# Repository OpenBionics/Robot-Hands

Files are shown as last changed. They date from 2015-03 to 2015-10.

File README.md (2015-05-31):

# Overview

OpenBionics is an initiative for the development of:
* open source
* affordable
* light-weight
* modular

robot hands and myoelectric prosthetic devices, that can be easily reproduced using off-the-shelf materials.

This repository contains all the necessary files, to replicate our robot hands.

For more information visit [OpenBionics.](http://www.openbionics.org/)

We have published a complete tutorial for the replication of our hands. The tutorial can be found [here.](http://www.openbionics.org/TR2015_OpenBionics_RobotHandsGuide.pdf)

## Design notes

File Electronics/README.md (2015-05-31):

# Electronics

This folder presents the electronics for the robot hands and for the interfaces (the Schematic, the PCB Layout and the OpenBionics library).
In order to control the RC or the AX12 servo motor, we use the arduino Micro Pro microcontroller platform, combined with a custom "Shield".

More information about Arduino Micro can be found [here.](http://arduino.cc/en/Main/ArduinoBoardMicro)

# Pinout
The Pin Mapping of the Arduino Micro Pro "Shield".



# Build of Materials of main PCB
	Part           Value              Device             Package 
	ARDUINO_MICRO  -                  -		     -
	C1             100u               CPOL-EUE2.5-6      E2,5-6  
	IC1            74LS241N           74LS241N           DIL20 
	J1             -                  HEADER-2X3P-2.54   -
	J2             SCREW-TERMINAL-2P  SCREW-TERMINAL-2P  -
	J3             -                  HEADER-2P-65/35MIL -          
	J4             -                  HEADER-2P-65/35MIL -    
	R1             10k                RESISTOR1206       1206
	R2             10k                RESISTOR1206       1206
	R3             10k                RESISTOR1206       1206
	S1             -                  SWITCH-SPDTSMD2    -  

# Mount PCB in to Robot Hands

You can attach the PCB at the PCBMount.STL part of the robot hands, using two M2x8 screws and two M2 nuts.



# Interfaces

#####RobotHandExtension
This interface requires push buttons and wires with the appropriate terminals.
The push buttons are placed in suitable pockets in RobotHandExtension part. Moreover, the  RobotHandExtension part has the necessary routing for the wires. The open button pin is B1 and it is placed on the top of the RobotHandExtension part. The close button pin is B2 and it is placed on the right hand side of the same part.

######Build of Materials
    2x push buttons
    2x wires terminals for HEADER-2P-65/35MIL (HEADER-2P)

#####SliderBox
This interface requires one arduino board and two linears potentiometers.
The potentiometers are connected to the analog inputs A0 and A1 of arduino board.

######Build of Materials
    2x linear potentiometer 10k (linear)
    1x Arduino board
    1x Jumper Wire Pack

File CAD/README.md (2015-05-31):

# Robot Hands CAD files

In this folder we provide appropriate 3D models (Solidworks .SLDASM .SLDPRT), laser cut files (.dxf) and files for 3d printer (.stl)
in order to replicate the proposed designs.

# Design and Fabrication Parameters

The designs of parts (Solidworks .SLDASM .SLDPRT) are parametric. Thus, the user could choose the appropiate dimensions that he wants.
A guide by which inspired is [here](http://www.eng.yale.edu/grablab/openhand/OpenHand%20CAD%20Guide.pdf). The picture below and tables
show the parameters and limits of the values. 



#####Design Parameters
	Name of parameter: limits, default value
	Width of Phalanxs, Wph (mm): 16 - 30, 20
	Length of Proximal Phalanx, Lp (mm): 24 - , 40
	Length of Distal Phalanx, Ld (mm): 18 - , 35
	Transmission radii of Proximal, rp (mm): 7.8 - , 8
	Transmission radii of Distal, rd (mm):7.8 - , 8
	Thickness of Proximal Flexure Joint, Tjointp (mm): 2 - 6, 4
	Thickness of Distal Flexure Joint, Tjointd (mm): 2 - 6, 5
	Length of Proximal Flexure Joint, Ljointp (mm): 6 - 16, 10
	Lenght of Distal Flexure Joint, Ljointd (mm): 6 - 16, 10
	Width of flexure Joints, Wjoint (mm): 16 - 30, 20
	Initial angle between Finger Base and robot Base, Tb (degrees): 20 - 45, 45
	Initial angle between Finger Base and Proximal, Tp (degrees): 0 - 30, 8
	Initial angle between Proximal and Distal, Td (degrees): 0 - 30, 8
	Finger opposition length, Lb (mm): 45 - 55, 45

#####Fabrication Parameters
	print fit, print_fit (mm): 0.2
	print free, print_free (mm): 0.45
	cut free, cut_free (mm): 0.2
	radii fit, radii_fit (mm): 0.2

In order to print or cut the parts in correct dimensions is necessary to add in design the above parameters.

More information about the fabrication parameters you can find [here for 3d printer](http://www.eng.yale.edu/grablab/openhand/OpenHand%20CAD%20Guide.pdf) and [here for laser cutter](http://support.ponoko.com/entries/498833-How-to-make-interlocking-acrylic-designs).

# Robot Finger Structure


# Replicating the Robot Hand Design

In order to replicate this design of robot hands, you will need the below materials.

    [1] 2mm Acrylic Parts or 3D printed Parts
	[2] Fasteners 
	[3] Cotton Swabs 
	[4] Silicone sheets 
	[5] Dyneema Fishing Line 
	[6] Rubber Foam tape 
	[7] Anti-Slip Tape 
	[8] Self-Adhesive Tape
	[9] Long Darners 
	[10] Nylon Fishing Line (not shown in the image)
	


For more information about [design](http://www.openbionics.org/?page_id=38)

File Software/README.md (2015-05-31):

# Introduction

<p style='text-align: justify;'>
In order to control the robot hand, we use the Robot Operating System (ROS) and arduino micro board.
The Planner PC runs one ROS node (RobotHand.py), that is responsible for sending commands, for parsing the data packages which are send by 
arduino micro and for publishing the received information in the ROS topics.
The arduino micro is responsible to parse the planner pc commands, to drive the different servo motors and is respond to the planner pc with
the information about robot hand.
</p>

# ROS Installation

Install this ROS package placing the folder in the /src directory of your ROS workspace. Build the package using the following command:

    $catkin_make

You have successfully installed the package. Make sure that all files are executable, using the following command:

     $chmod +x RobotHand.py

# Arduino Installation

Donwload the [arduino IDE](http://arduino.cc/en/main/software).
Place the [library for dynamixel servo](https://github.com/OpenBionics/Robot-Hands/tree/master/Software/Arduino/Libraries/DynamixelSerial) in 
your library folder. 
Place the RobotHand folder in your arduino workspace.
Open the RobotHand.ino with arduino IDE.
Select with MODE definition the servo motor that you use:

    #define MODE 1 :is for stadard RC servo
    #define MODE 2 :is for dynamixel AX12 servo

Upload the program to the arduino Micro board.

# How to run ROS node

To run this ROS package, you have to run the launch file:

    $roslaunch openbionics RobotHand.launch

In the launch file you can set up the USB port, to establish serial communication with the robot hand. It is necessary to give write permissions
on that port. The RobotHand node listen to RobotHandCmd topic and send those commands to arduino board via serial. The robot hand responds with 
sending back to the host pc the acknowledgement and the state of servo motor (depending to the sending command). The RobotHand node publish the 
acknowledgment in the RobotHandAck topic and the state of motor in MotorState topic.
If the acknowledgment is 0 means that robot hand receives acceptable command, but if it is -1 means that you have send wrong command. The motor 
state package has the following format:
    
    acknowledgment;angle (deg);load (0-1023 for CCW, 1024-2047 for CW)\n

# How to control the robot hand

To control the robot hand you can use the following command:

    $rostopic pub -1 /RobotHandCmd openbionics/Command "cmd: 'arg'" 

Replace the arg: 

    ps "angle in deg", the angle depends on the servo motor
    vl "velocity in deg/s", the velocity depends on the servo motor
    gs, to get the state of servo motor

In order to view the acknowledgment and the state of motor you can use the following commands:

	$rostopic echo /MotorState
	$rostopic echo /RobotHandAck

# Interfaces

It is not necessary to use the planner PC for the control of the robot hand. The user could also use the proposed interfaces.

#####RobotHandExtension
The firmware for RobotHandExtension interface is inside in RobotHand.ino and is active:

    #define EXTENSION 1: with RobotHandExtension interface 

and deactive:

    #define EXTENSION 0: without RobotHandExtension interface

#####SliderBox
The SliderBox interface requires the use of planner PC. The ROS node that reads the commands from SliderBox writes in RobotHandCmd topic.
Also, with this interface an additional arduino is needed. The firmware for arduino is placed in Arduino/SliderBox.
In order to run SliderBox ROS node, make sure that it is executable, using the following command:

     $chmod +x SliderBox.py

and run it:

    $rosrun openbionics SliderBox.py "usb port" (e.g /dev/ttyACM0)

Before you execute the above command, you must run the launch file as mentioned above (How to run ROS node), and to give write
permissions on that port.

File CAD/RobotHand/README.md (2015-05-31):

# Physical Characteristics of Robot Finger and Hand
###Robot Finger:


    DOF's: 2
	Width(mm): 20
	Lenght(mm): 95
	Weigth(g): 20 
	Force in fingertip (N): 8
	
###Robot Hand:


	Actuators: 1
	Base Height(mm): 100-110
	Base Width(mm): 77
	Weight(g): 280
	Number of Fingers: 2-4

To change the design or fabrication parameters you must change the dimensions of the RobotHandParameters.SLDPRT sketch.

A complete tutorial for the replication of this robot hand can be found
[here.](http://www.openbionics.org/TR2015_OpenBionics_RobotHandsGuide.pdf)

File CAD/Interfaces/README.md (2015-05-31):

# Robot Hands Interfaces
In order to control robot hands the user can use the proposed interfaces.
#####Robot Hand Extension: 
This interface had two buttons, one for closing and one for opening the robot hand. 
To make this, you should print with 3d printer two parts, RobotHandExtension.STL and dovetail_male_RobotHandExtension.STL.
For connecting the two parts you must use a M5 nut and screw which you can find at common parts folder.
######Build of Materials
    1x M5 Nut
    1x M5 L22
    ABS Filament

#####SliderBox:
This interface had two linear potentiometers. Until now the one of these are active.
Also, SliderBox could be use for robot hands which had two servo motors like
[Model T42  of Yale OpenHand Project](http://www.eng.yale.edu/grablab/openhand/model_t42.html#performance).
To make this, you should cut the parts, which are in /dxf folder, in acrylic sheet with laser cutter. For connecting the parts you must use 
glue for acrylic, M3 nuts and screws. For connecting the potentiometers in the
SliderBox you must use M3 nuts, screws and spacers which are in common parts folder. 
######Build of Materials
    14x M3 Nut
    6x M3 L8
    8x M3 L20
    8x plastic spacers L15 for M3 screw
    Glue for Acrylic
    Acrylic sheet 2mm
    
For both interfaces you can find the software, firmware and electronics in respective folders of Robot-Hands repo.

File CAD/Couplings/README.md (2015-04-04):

# Couplings

The designs of Mount_Kuka-Youbot.SLDPRT, dovetail_famele.SLDPRT and dovetail_made.SLDPRT are taken from [Yale Openhand Project](https://github.com/grablab/openhand-hardware/tree/master/couplings), thank you!

The design of MountPA10.SLDASM is specific for our flange for the Mitsubishi PA10 robotic arm.

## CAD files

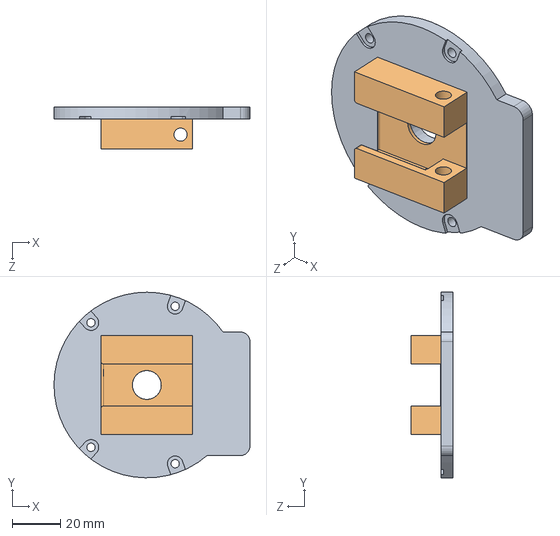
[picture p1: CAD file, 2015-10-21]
CAD/RobotHand/3d Printed/Robot Base/FlangeCoupling.SLDASM
81.3 x 77.0 x 17.5 mm
FlangePlate
dovetail_female

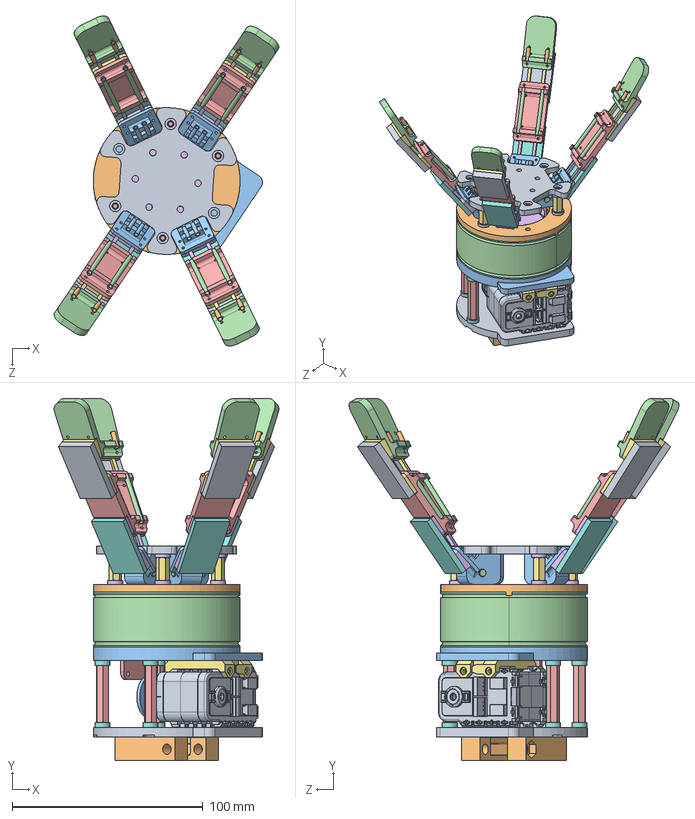
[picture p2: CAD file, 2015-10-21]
CAD/RobotHand/3d Printed/RobotHand.SLDASM
117.9 x 190.0 x 173.1 mm
TopPlate
MiddlePlate
BottomPlate
93600A129 - DowelPinM4L12 x 5
PCBMount
DifferentialDisk
AX12Base
ax12_wheel
ax12_box
ax12_cog
servoPulleyAX12
94868A181 - HexStandoffM3L30 x 8
Spacer - 2mm x 8
94868A007 - HexStandoffM3L12 x 4
Spacer - 2_5mm x 8
FlangePlate
dovetail_female
FingerBase x 4
FingerDIP x 4
FingerPIP x 4
JointBase1 x 4
JointBase2 x 4
Joint1 x 4
Joint2 x 4
tubeDIP x 8
tubeMCP x 8
tubePIP x 8

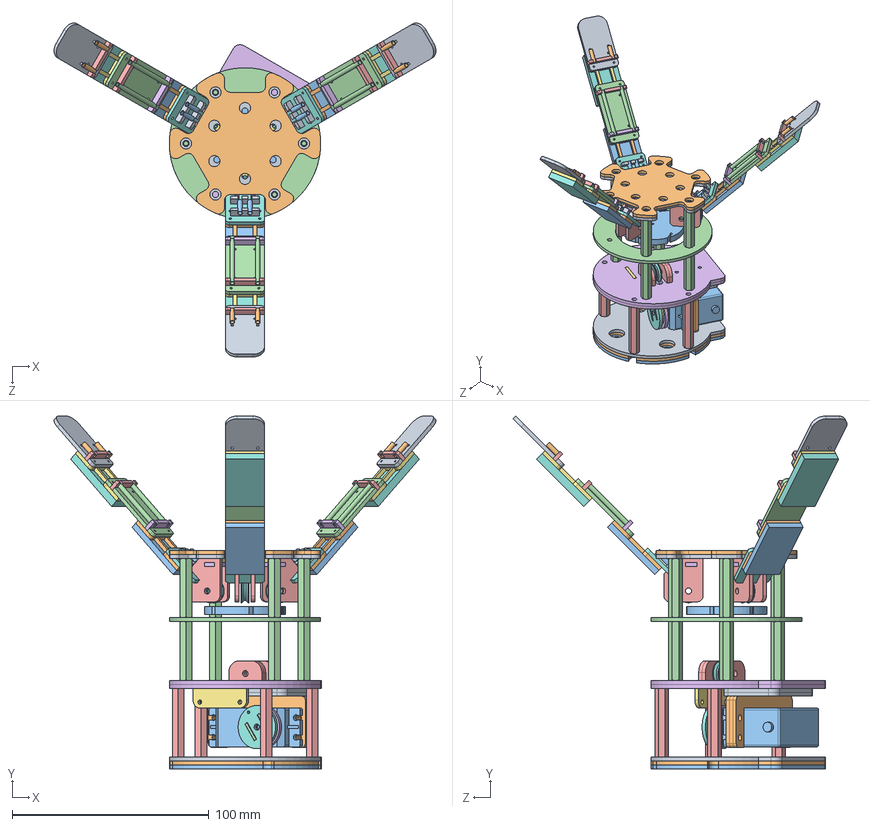
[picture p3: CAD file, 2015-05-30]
CAD/RobotHand/Laser Cutted/RobotHand.SLDASM
194.3 x 179.5 x 169.9 mm
TopPlate1
TopPlate2
DifferentialDisk
MiddlePlate
BearingBase x 4
BottomPlate x 2
PCBMount
pulley x 4
MountPA10_1
MountPA10_2
MountPA10_3
94868A181 - HexStandoffM3L30 x 8
94868A184 - HexStandoffM3L35 x 4
servoPulleyStd1
servoPulleyStd2
servoPulleyStd3
stdServoBase1 x 2
stdServoBase2 x 3
HS-422
ServoHorn
FingerBase1 x 6
FingerBase2 x 3
FingerBase3 x 3
FingerMCP x 3
TubePlateMCP x 6
JointBase1 x 3
Joint1 x 3
FingerPIP x 3
TubePlateDIP x 6
TubePlatePIP x 3
JointBase2 x 3
Joint2 x 3
FingerDIP x 3
tubeDIP x 6
tubeMCP x 6
tubePIP x 6

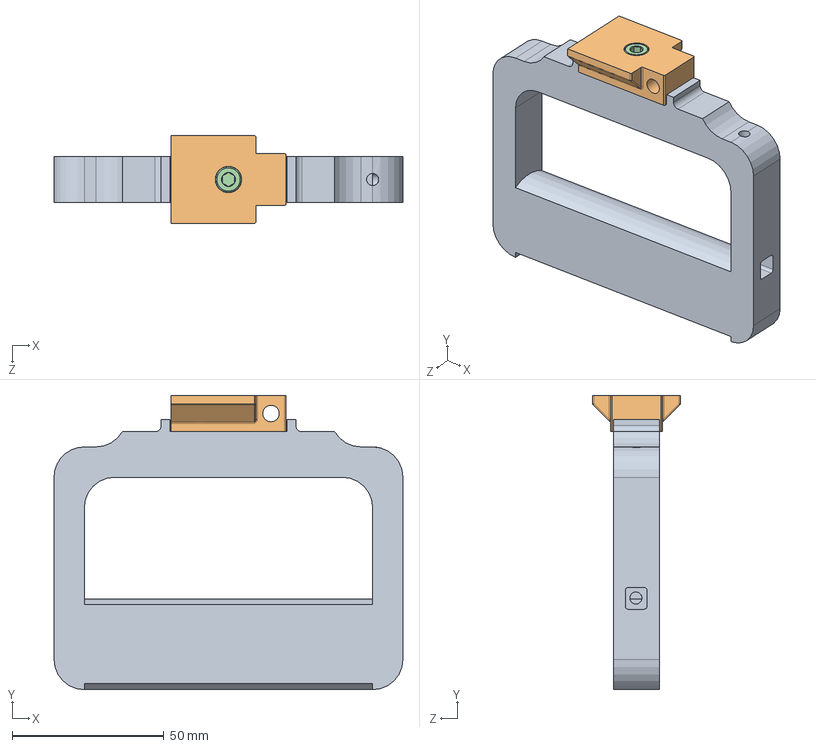
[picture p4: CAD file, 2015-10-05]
CAD/Interfaces/Extension/RobotHandExtensionAssembly.SLDASM
115.0 x 97.0 x 29.0 mm
RobotHandExtension
dovetail_male_RobotHandExtension
91828A241 - NutM5
92290A782 - ScrewM5L22

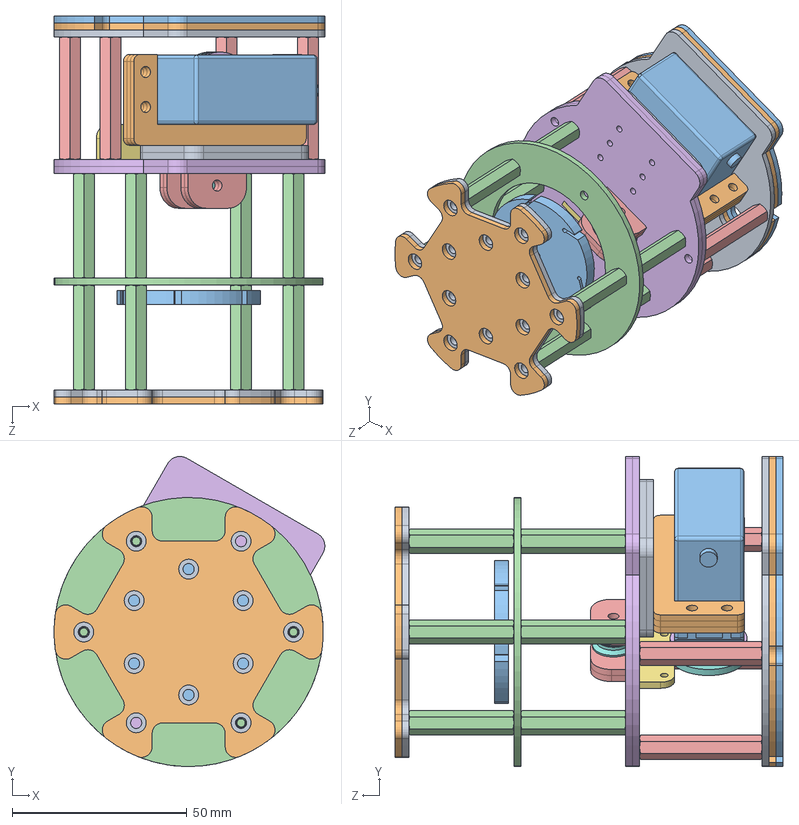
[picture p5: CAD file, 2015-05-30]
CAD/RobotHand/Laser Cutted/Robot Base/Base.SLDASM
77.5 x 88.8 x 111.0 mm
TopPlate1
TopPlate2
DifferentialDisk
MiddlePlate
BearingBase x 4
BottomPlate x 2
PCBMount
pulley
MountPA10_1
MountPA10_2
MountPA10_3
94868A181 - HexStandoffM3L30 x 8
94868A184 - HexStandoffM3L35 x 4
servoPulleyStd1
servoPulleyStd2
servoPulleyStd3
stdServoBase1 x 2
stdServoBase2 x 3
HS-422
ServoHorn

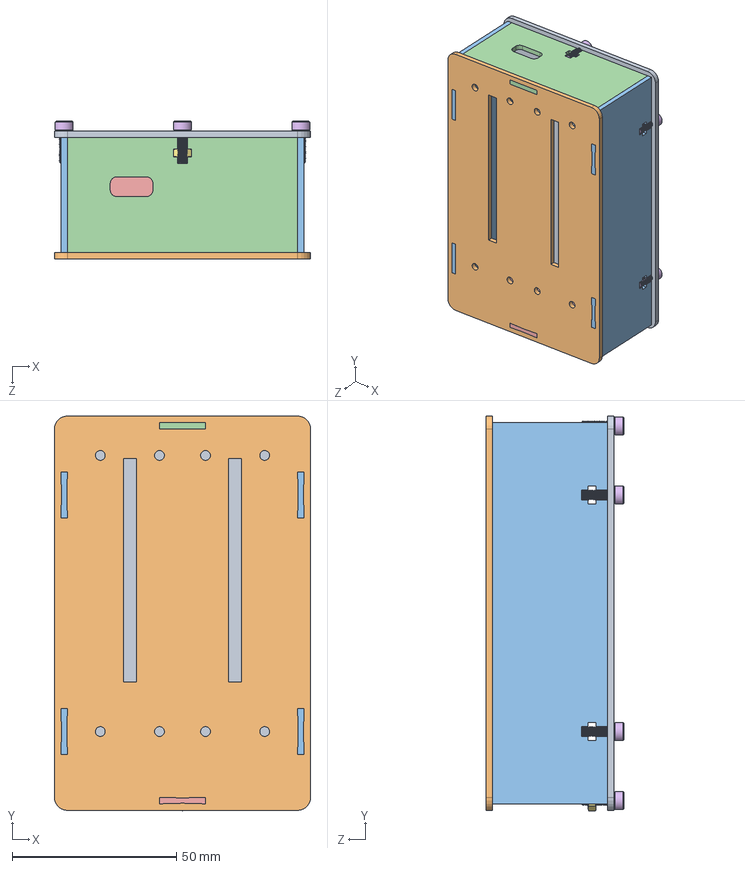
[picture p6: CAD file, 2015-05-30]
CAD/Interfaces/SliderBox/SliderBox.SLDASM
78.0 x 120.2 x 42.0 mm
SliderBottom
SliderTop
SlideSide x 2
SlideSideUp
SlideSideDown
92290A115 - ScrewM3L10 x 6
94150A325 - NutM3

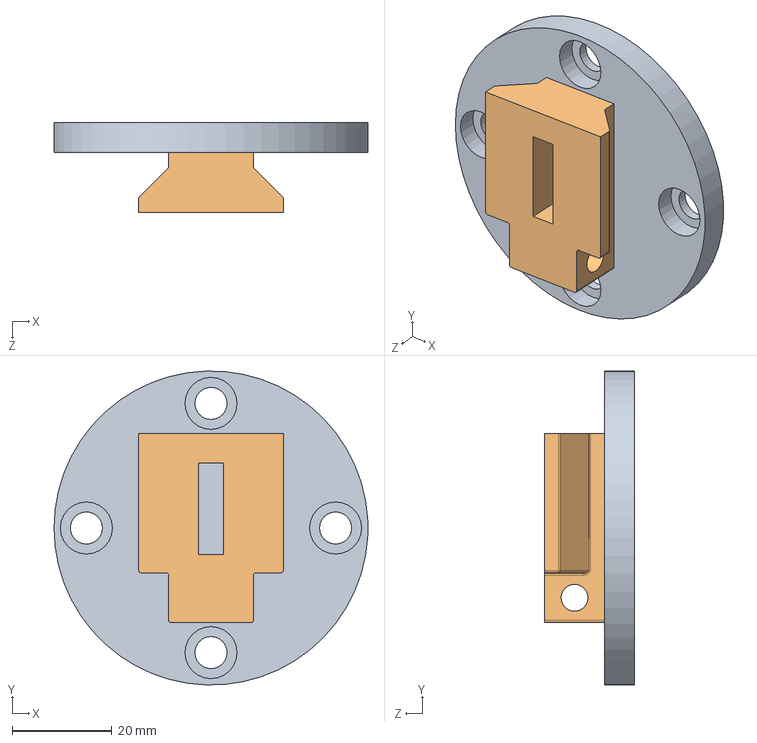
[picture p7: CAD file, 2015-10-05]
CAD/Couplings/MountPA10.SLDASM
63.0 x 63.0 x 18.0 mm
MountPlatePA10
dovetail_male

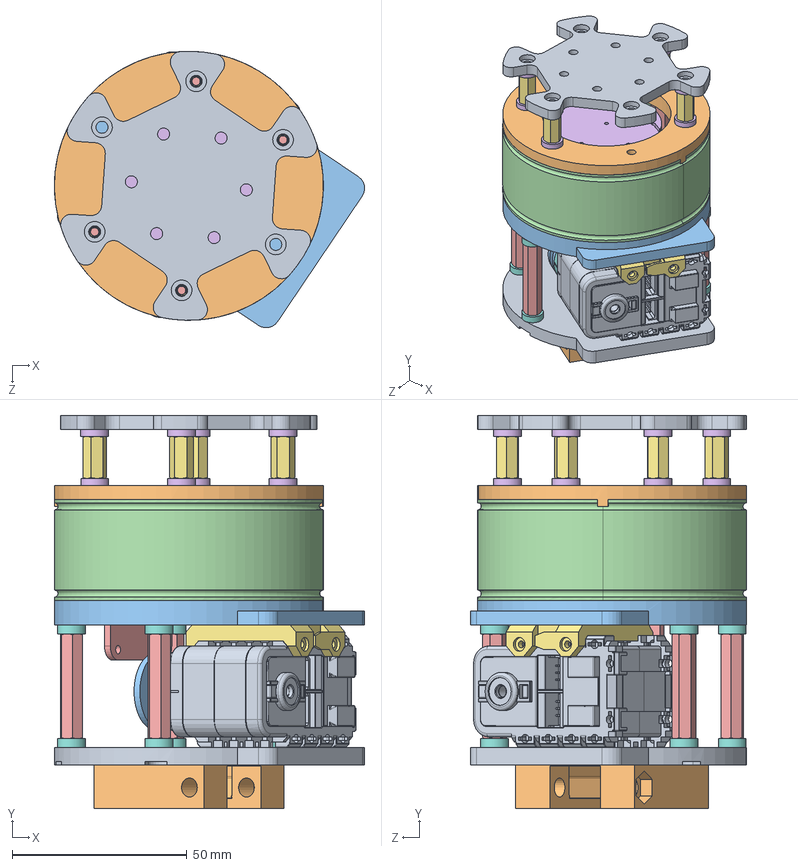
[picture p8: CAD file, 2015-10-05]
CAD/RobotHand/3d Printed/Robot Base/Base.SLDASM
88.8 x 112.5 x 79.1 mm
TopPlate
MiddlePlate
BottomPlate
93600A129 - DowelPinM4L12
PCBMount
DifferentialDisk
AX12Base
ax12_wheel
ax12_box
ax12_cog
servoPulleyAX12
94868A181 - HexStandoffM3L30 x 8
Spacer - 2mm x 8
94868A007 - HexStandoffM3L12 x 4
Spacer - 2_5mm x 8
FlangePlate
dovetail_female

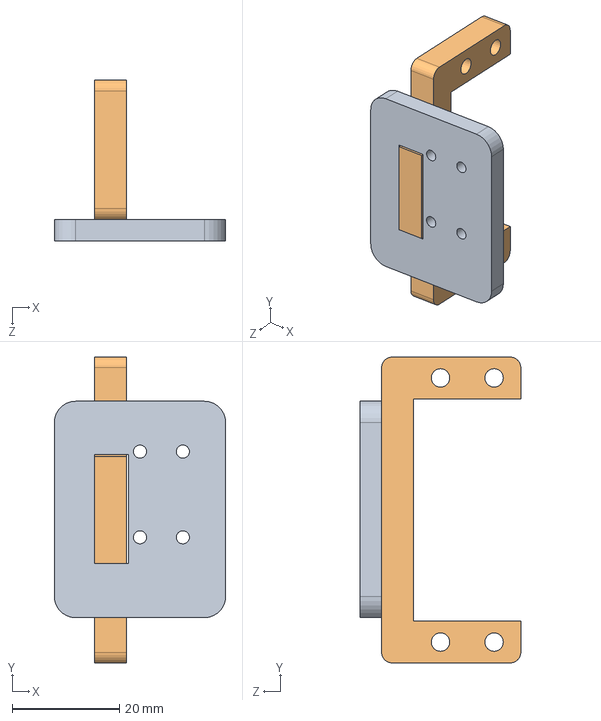
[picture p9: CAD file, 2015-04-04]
CAD/RobotHand/3d Printed/Robot Base/stdServoBase.SLDASM
32.0 x 57.1 x 30.0 mm
stdServoBase1
stdServoBase2

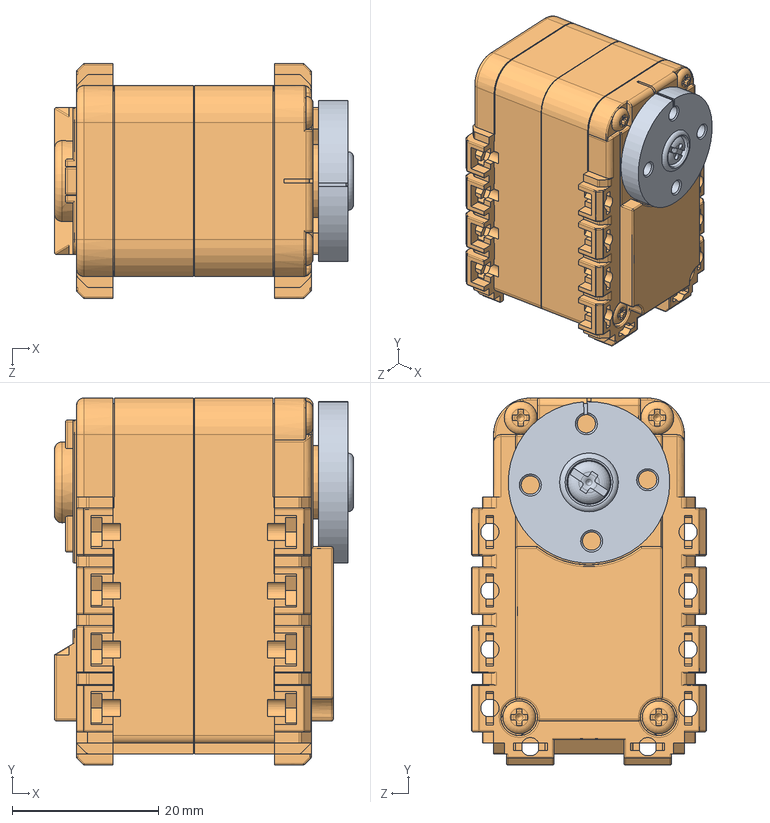
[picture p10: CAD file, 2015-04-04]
CAD/Common Parts/AX12.SLDASM
40.8 x 50.0 x 32.0 mm
ax12_wheel
ax12_box
ax12_cog

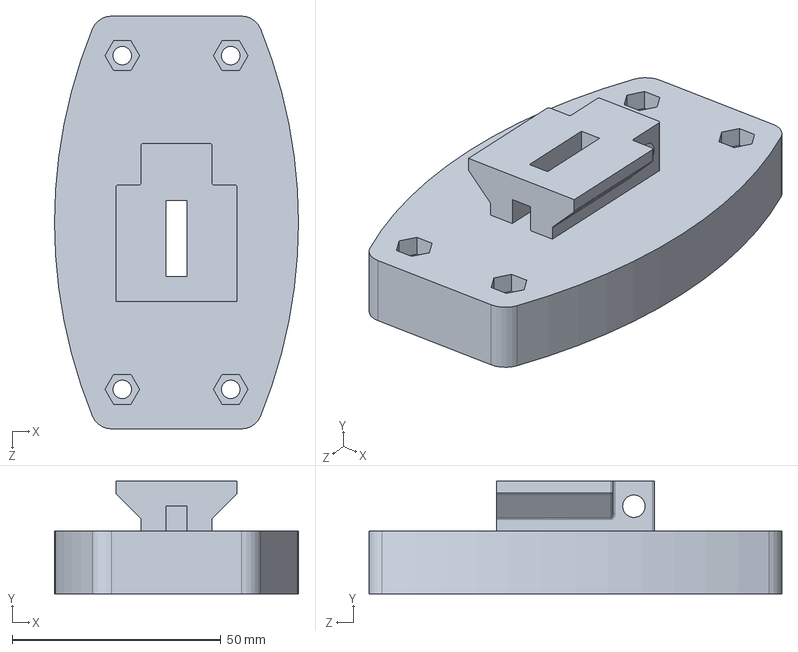
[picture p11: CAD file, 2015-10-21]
CAD/Couplings/Mount_Kuka-Youbot.SLDPRT
58.5 x 27.0 x 99.0 mm

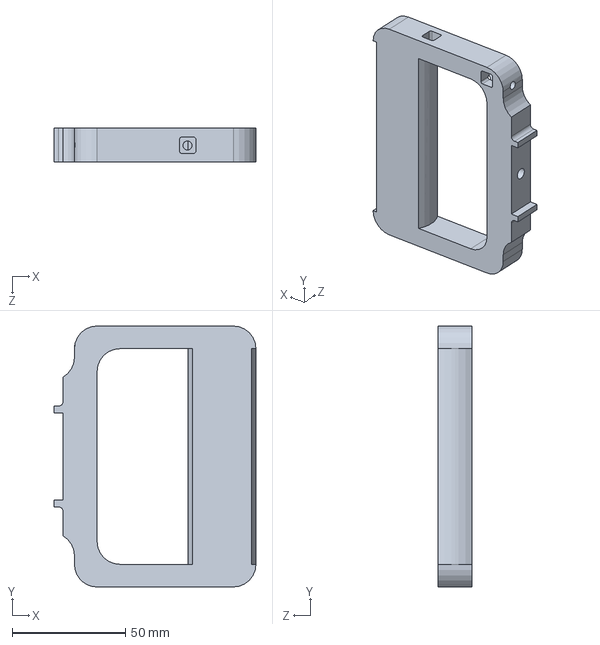
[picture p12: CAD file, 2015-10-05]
CAD/Interfaces/Extension/RobotHandExtension.SLDPRT
89.0 x 115.0 x 15.0 mm

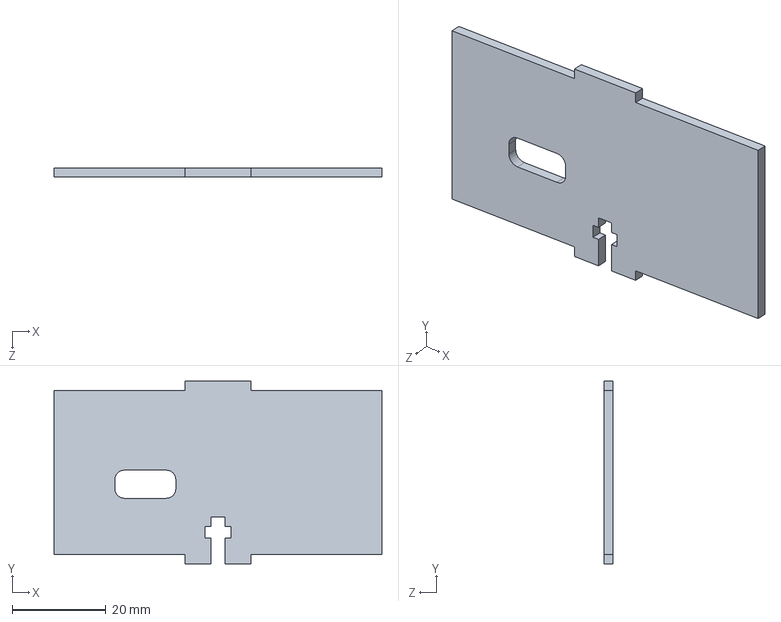
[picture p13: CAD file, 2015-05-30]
CAD/Interfaces/SliderBox/SlideSideUp.SLDPRT
70.0 x 39.0 x 2.00 mm

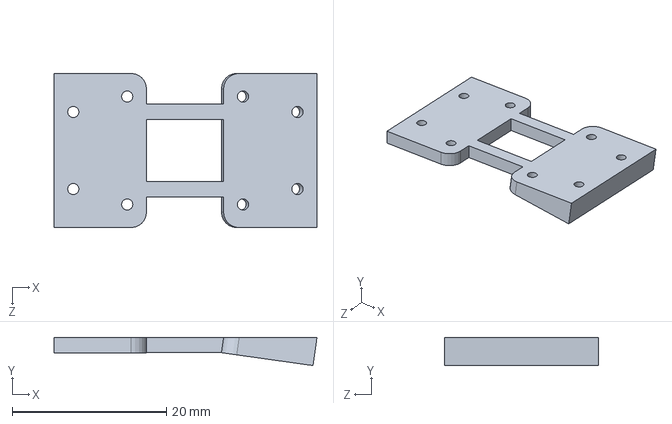
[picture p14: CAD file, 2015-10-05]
CAD/RobotHand/3d Printed/Robot Finger/JointBase2.SLDPRT
34.1 x 3.65 x 20.0 mm

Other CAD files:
CAD/FabricationParameters.SLDPRT
CAD/RobotHand/Laser Cutted/Robot Base/TopPlate1.SLDPRT
CAD/RobotHand/Laser Cutted/Robot Finger/FingerBase3.SLDPRT
CAD/RobotHand/RobotHandParameters.SLDPRT
CAD/Common Parts/90666A131 - ScrewM6L12LowProfile.SLDPRT
CAD/Common Parts/90965A130 - WasherM3.SLDPRT
CAD/Common Parts/91290A123 - ScrewM3L20.SLDPRT
CAD/Common Parts/91292A114 - ScrewM3L12.SLDPRT
CAD/Common Parts/91292A195 - ScrewM5L45.SLDPRT
CAD/Common Parts/91292A831 - ScrewM2L6.SLDPRT
CAD/Common Parts/91292A832 - ScrewM2L8.SLDPRT
CAD/Common Parts/91292A833 - ScrewM2L10.SLDPRT
CAD/Common Parts/91828A241 - NutM5.SLDPRT
CAD/Common Parts/92290A113 - ScrewM3L8.SLDPRT
CAD/Common Parts/92290A115 - ScrewM3L10 .SLDPRT
CAD/Common Parts/92290A745 - ScrewM2L4.SLDPRT
CAD/Common Parts/92290A782 - ScrewM5L22.SLDPRT
CAD/Common Parts/92605A109 - NonmarringM3L20.SLDPRT
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

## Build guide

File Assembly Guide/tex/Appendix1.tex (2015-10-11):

\section{Necessary Tools and Materials}

In this section we present the necessary tools and materials for the construction and assembly of the different robot hand parts. All tools and materials used, can be easily found in hardware stores around the world.

\begin{center}
\begin{tikzpicture}
\node [mybox] (box){
	\begin{tabular}{ c c }
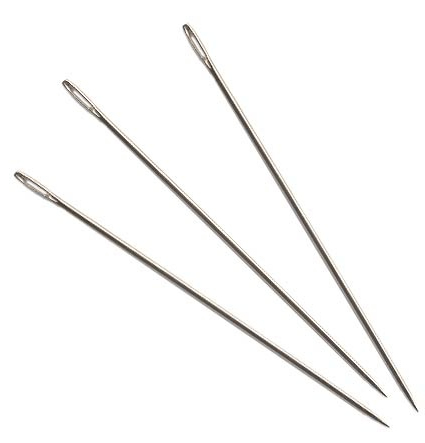
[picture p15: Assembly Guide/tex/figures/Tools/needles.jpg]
		 &
		 
		\\
		Long Darners [D:1mm, L:70mm] & Precision Ruler
		\\
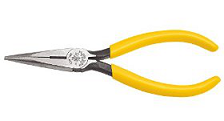
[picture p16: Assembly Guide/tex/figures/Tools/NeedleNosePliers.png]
		 &
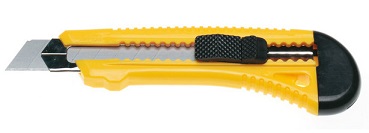
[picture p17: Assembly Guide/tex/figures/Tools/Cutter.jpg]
		 
		\\
		 Long-Nose Pliers with Side-Cutting & Cutter
		\\
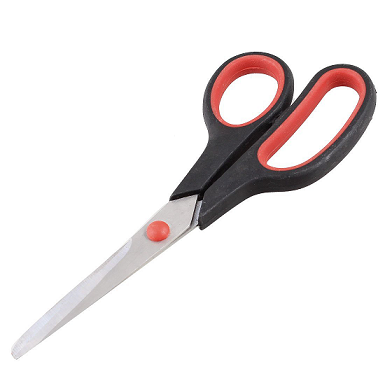
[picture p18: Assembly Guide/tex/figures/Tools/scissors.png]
		 &
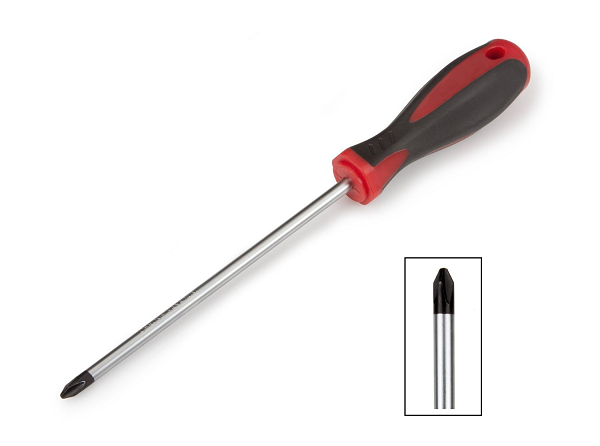
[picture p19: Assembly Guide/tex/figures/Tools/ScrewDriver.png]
		
		\\
		Scissors & Phillips Screwdriver [no. 1,2]
		\\
		 &
		
		\\
		Open-End Wrench [M2, M3 Hex Nut] & Allen Wrench [2.5mm]		
		\\
    	\end{tabular}
};
\node[mytitle, right=10pt] at (box.north west) {Tools};
\end{tikzpicture}%
\end{center}

\begin{center}
\begin{tikzpicture}
\node [mybox] (box){
	\begin{tabular}{ c c c }
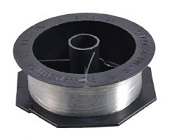
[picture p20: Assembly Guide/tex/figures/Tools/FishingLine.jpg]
		 &
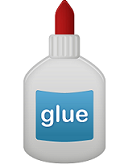
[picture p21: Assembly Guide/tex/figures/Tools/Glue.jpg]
                 &
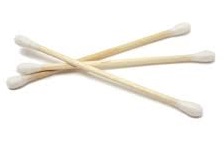
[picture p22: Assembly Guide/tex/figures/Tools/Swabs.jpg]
                \\
		Dyneema Fishing Line [0.4mm] & Acrylic Glue \& Super Glue & Ear Cotton Swabs\\
		\& Nylon Fishing Line [0.4mm] & & \\
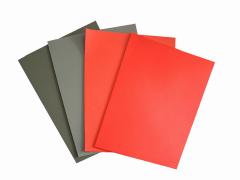
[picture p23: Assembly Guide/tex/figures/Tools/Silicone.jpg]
		 &
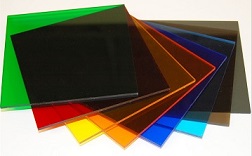
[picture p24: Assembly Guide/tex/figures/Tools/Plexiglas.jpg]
                 & 
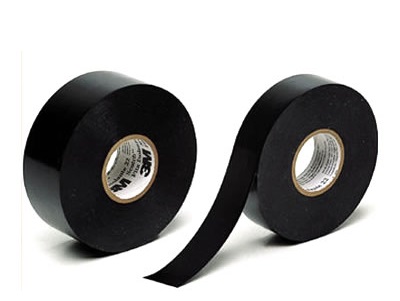
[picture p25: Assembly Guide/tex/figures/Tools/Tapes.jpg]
                
                \\
		Silicone Sheets [3mm, 4mm] & Plexiglas Sheets [2mm, 4mm] & Sponge, Self-Adhesive \\
		& & \& Anti-Slip Tapes \\
    	\end{tabular}
};
\node[mytitle, right=10pt] at (box.north west) {Materials};
\end{tikzpicture}%
\end{center}

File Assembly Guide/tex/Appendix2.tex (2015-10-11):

\section{Parts Reference}

In this section we list all the necessary parts for the assembly of the robot hand. The parts are divided in two categories: i) the robot finger parts and ii) the robot base parts. The second category contains the parts for the AX12 Dynamixel servo base, as well as a second base for a standard RC servo, like the Hitec HS-311. The parts that can be constructed using a 3D-printer, are presented in section 5.4.  As you can see below, the three tables contain the names of the Solidworks part files, as well as their quantity and usage. To facilitate the identification of each part, we also provide images of the models. 

\subsection{Robot Finger}

\begin{table}[h!]
\centering
\scalebox{0.9}{
	\begin{tabular}{ | l | l | l |}
	\hline
 	\multicolumn{3}{|c|}{\bf{Robot Finger}} \\
	\hline
	{\bf{Part Name}} & {\bf{Qty}} & {\bf{Description}}\\ \hline
	FingerBase1 & 8 &Acrylic Part for Finger Base   \\ \hline
    	FingerBase2 & 4 & Acrylic Part for Finger Base \\ \hline
    	FingerBase3 & 4 & Acrylic Part for Finger Base \\ \hline
    	FingerMCP & 4 & Acrylic Part for MCP \\ \hline
    	FingerPIP &  4 & Acrylic Part for PIP\\ \hline
    	FingerDIP &  4 & Acrylic Part for DIP \\ \hline
    	TubeplateMCP & 8 & Acrylic Part for Base of Tubes for MCP\\ \hline
    	Tubeplate & 12 &  Acrylic Part for Base of Tubes for Phalanges\\ \hline
    	tubeMCP & 8 & Cotton Swab Tube for MCP [d:2mm, D:2.5mm, L:8mm]  \\ \hline
    	tubePIP & 8 & Cotton Swab Tube for PIP [d:2mm, D:2.5mm, L:26mm]  \\ \hline
    	tubeDIP & 8 & Cotton Swab Tube for DIP [d:2mm, D:2.5mm, L:10mm]  \\ \hline
	Joint1 & 4 & Silicone Sheet, 60A Durometer  [(35x18x3)mm]\\ \hline
    	Joint2 & 4 & Silicone Sheet, 60A Durometer [(39x18x4)mm]\\ \hline
    	M3Washer &  20 & Fastener \\ \hline
	M3x12 &  8 &  Fastener  \\ \hline
    	M3Nut &  9 & Fastener \\ \hline
    	pulley & 4 & V-Groove Sealed Ball Bearing [d:3mm, D:12mm, B:4mm, Deepness:1.2mm] \\ \hline
	Dyneema Fishing Line & 1 & Tendon Routing [D:0.4mm, Strength:41.5kg] \\ \hline
	Rubber Foam Tape & 1 & [Width:10mm, Thickness:4mm] \\ \hline
	Anti-Slip Tape & 1 & 3M Gripping Material [Width:25mm] \\ \hline
	Self-Adhesive Tape & 1 & 3M Scotch 23 [Width:20mm] \\ \hline
    	\end{tabular}
}
\end{table}

\newpage

\begin{center}
\begin{tikzpicture}
\node [mybox] (box){%
	\begin{tabular}{ c c c c}
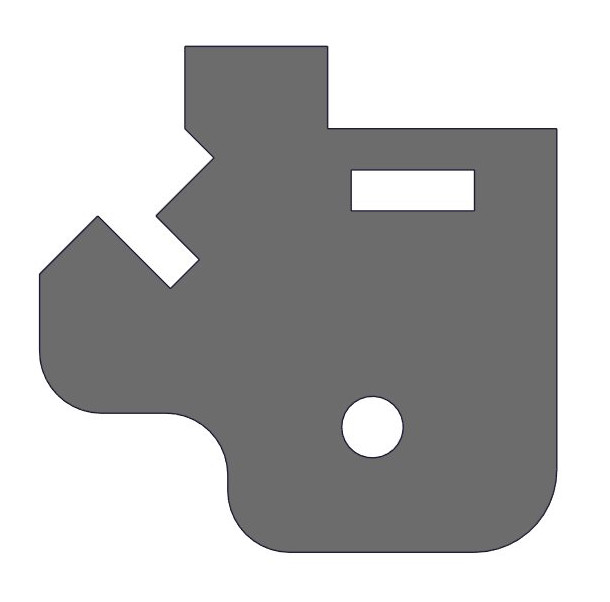
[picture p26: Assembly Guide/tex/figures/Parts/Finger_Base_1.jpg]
		 &
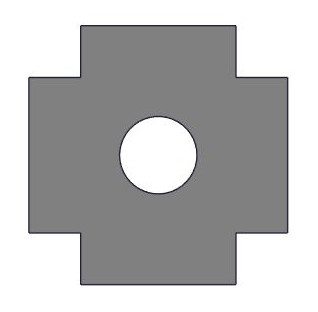
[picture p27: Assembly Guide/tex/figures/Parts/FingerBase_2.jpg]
		 &
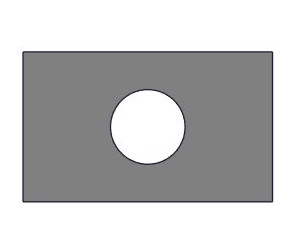
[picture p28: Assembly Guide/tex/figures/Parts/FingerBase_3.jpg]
			&
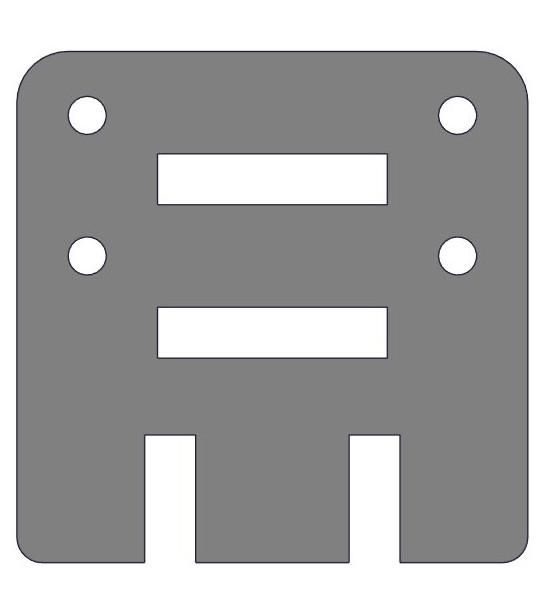
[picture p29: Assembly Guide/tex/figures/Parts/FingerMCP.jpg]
		 \\
		FingerBase1 &  FingerBase2 & FingerBase3 & FingerMCP \\ \\
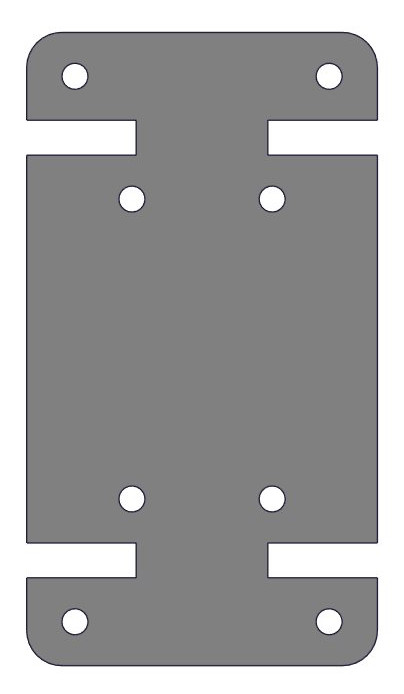
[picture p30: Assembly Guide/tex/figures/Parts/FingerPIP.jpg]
		 &
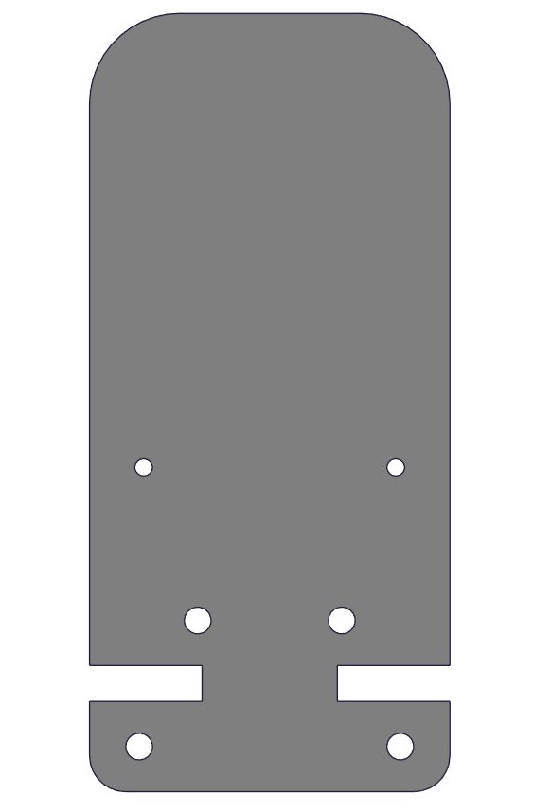
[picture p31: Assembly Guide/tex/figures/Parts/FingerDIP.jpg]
		 &
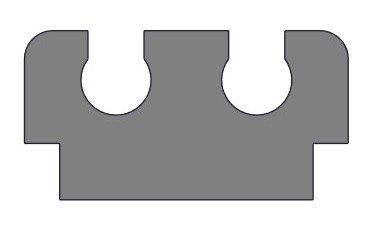
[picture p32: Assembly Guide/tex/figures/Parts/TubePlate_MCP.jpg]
		 &
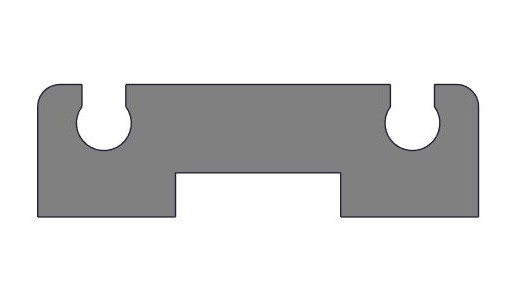
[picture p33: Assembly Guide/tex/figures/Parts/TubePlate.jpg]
		 \\
		FingerPIP & FingerDIP & TubeplateMCP & Tubeplate \\ \\
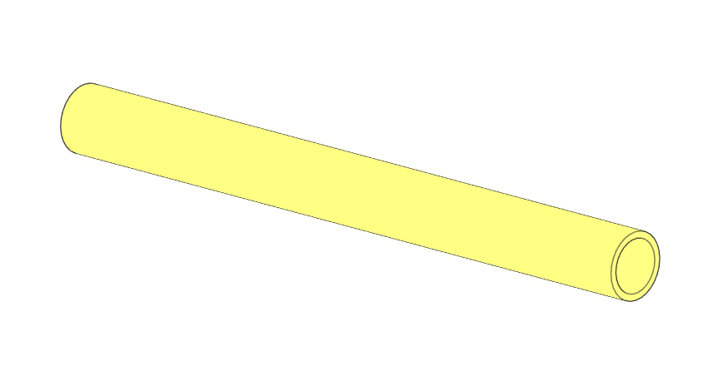
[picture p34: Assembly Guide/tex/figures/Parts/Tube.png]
		 &
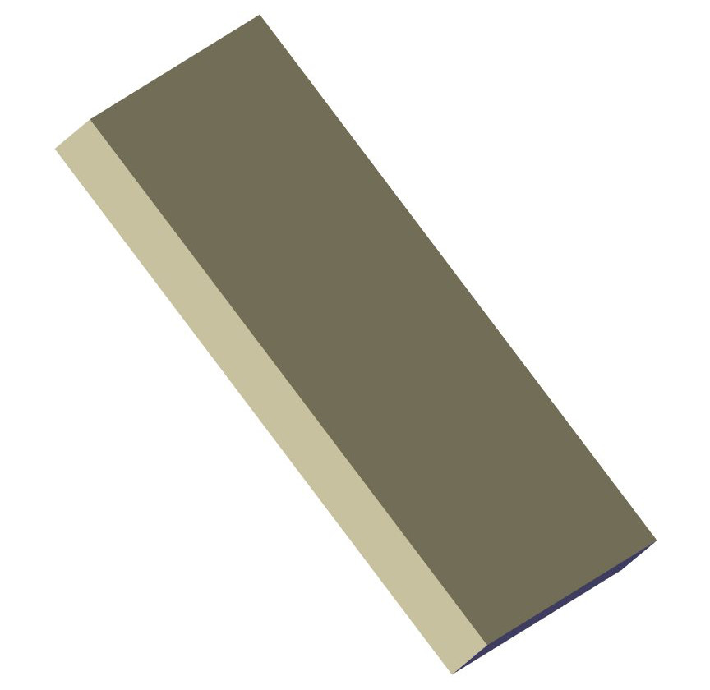
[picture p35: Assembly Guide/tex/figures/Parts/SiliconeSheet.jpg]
		 &
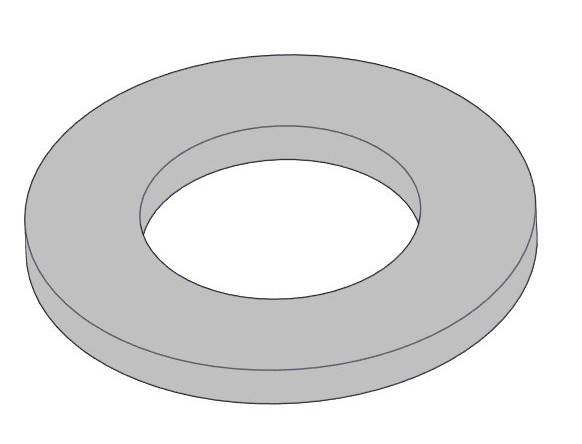
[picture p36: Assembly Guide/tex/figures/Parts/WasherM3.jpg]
		 &
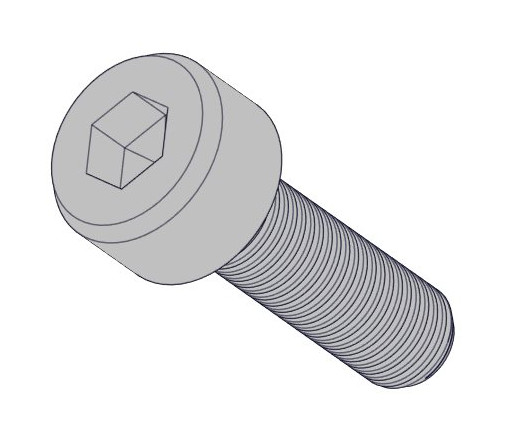
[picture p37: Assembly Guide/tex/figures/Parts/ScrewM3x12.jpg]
		 \\
		tubes &  Joint1, Joint2 & M3Washer & M3x12 \\ \\
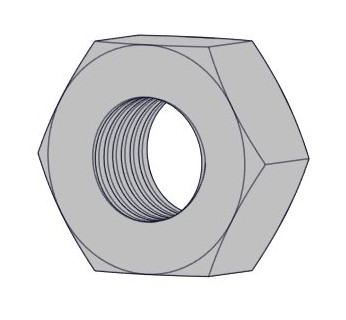
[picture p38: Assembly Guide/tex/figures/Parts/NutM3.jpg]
		 &
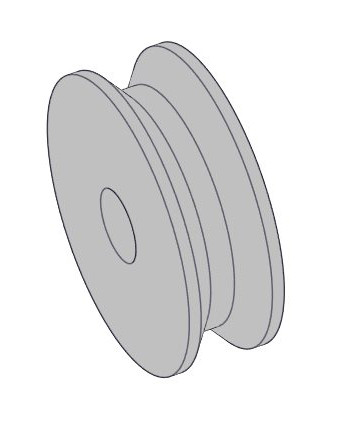
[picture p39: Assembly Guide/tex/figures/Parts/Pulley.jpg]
		 \\
		M3Nut & pulley  \\ \\
    	\end{tabular}
};
\node[mytitle, right=10pt] at (box.north west) {Parts};
\end{tikzpicture}%
\end{center}

\newpage

\subsection{Robot Hand Base for AX12 Servo}

\begin{table}[h!]
\centering
\scalebox{0.8}{
	\begin{tabular}{ | l | l | l |}
	\hline
 	\multicolumn{3}{|c|}{{\bf{Robot Hand Base for AX12 Servo}}} \\
	\hline
        {\bf{Part Name}} & {\bf{Qty}} & {\bf{Description}}\\ \hline
    	TopPlate & 2 & Acrylic Part of Robot Hand Base  \\ \hline
    	MiddlePlate & 1 & Acrylic Part of Robot Hand Base\\ \hline
    	DifferentialDisk & 2 & Acrylic Part of Differential Mechanism \\ \hline
    	BottomPlateAX12& 2 & Acrylic Part of Robot Hand Base \\ \hline
    	BearingBase & 4 & Acrylic Part of Robot Hand Base \\ \hline
    	AX12Base & 1 & Acrylic Part of Actuator Base \\ \hline
    	flangeAX12 \#1 & 1 & Acrylic Part of Flange \\ \hline
    	flangeAX12 \#2 & 1 & Acrylic Part of Flange \\ \hline
    	flangeAX12 \#3 & 1 & Acrylic Part of Flange \\ \hline
    	servoPulleyAX12 \#1 & 1 & Acrylic Part of Actuator Pulley \\ \hline    	
    	servoPulleyAX12 \#2 & 1 & Acrylic Part of Actuator Pulley \\ \hline
    	servoPulleyAX12 \#3 & 1 & Acrylic Part of Actuator Pulley \\ \hline
    	PCBMount & 1 & Acrylic Part for PCB \\ \hline    	    	    	    	
	Dyneema Fishing Line & 1 & Tendon Routing [D:0.4mm, Strength:41.5kg] \\ \hline
	Rubber Foam Tape & 1 & Tape for Fingertips [Width:10mm, Thickness:4mm] \\ \hline
	Anti-Slip Tape & 1 & 3M Gripping Material [Width:25mm] \\ \hline
    	AX12 & 1 & Robotis Actuator Dynamixel AX-12A  \\ \hline
    	pulley & 1 & V-Groove Sealed Ball Bearing [d:3mm, D:12mm, B:4mm, Deepness:1.2mm] \\ \hline
    	PlasticSpacer & 2 & Fastener [d:3.1mm, D:6mm, L:2mm] \\ \hline
    	M3Spacer30 & 8 & Fastener, Spacer M3 [L:30mm] \\ \hline
    	M3Spacer25 & 4 & Fastener, Spacer M3 [L:25mm] \\ \hline
    	M3Spacer10 & 4 & Fastener, Spacer M3  [L:10mm] \\ \hline
	M3ThreadedRod & 4 & Fastener, M3 Threaded Rod [L:20mm] \\ \hline	
    	M3x10 & 16 & Fastener, M3 [L:10mm] \\ \hline
    	M3x20 & 1 & Fastener, M3 [L:20mm] \\ \hline
    	M3Washer &  13 & Fastener, M3 [D:7.5, L:0.5mm] \\ \hline
    	M3Nut &  1 & Fastener, M3 Hex Nut \\ \hline
    	M2x8 & 8 & Fastener, M2 [L:8mm] \\ \hline
    	M2x6 & 2 & Fastener, M2 [L:6mm] \\ \hline
    	M2Nut & 8 & Fastener, M2 Hex Nut \\ \hline
	M2.5x15 & 1 & Fastener, M2.5 for AX12 [L:15mm] \\ \hline
    	\end{tabular}
}
\end{table}

\vspace{0.2cm}

\begin{center}
\begin{tikzpicture}
\node [mybox] (box){%
	\begin{tabular}{ c c c c}
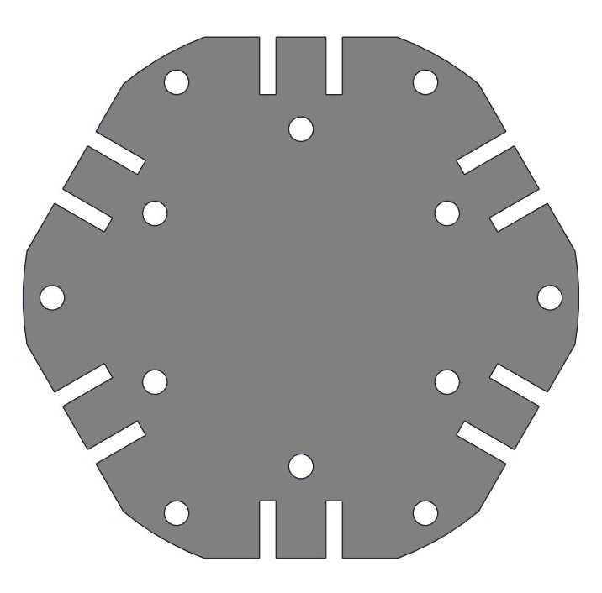
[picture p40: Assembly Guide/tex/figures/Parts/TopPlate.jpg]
		 &
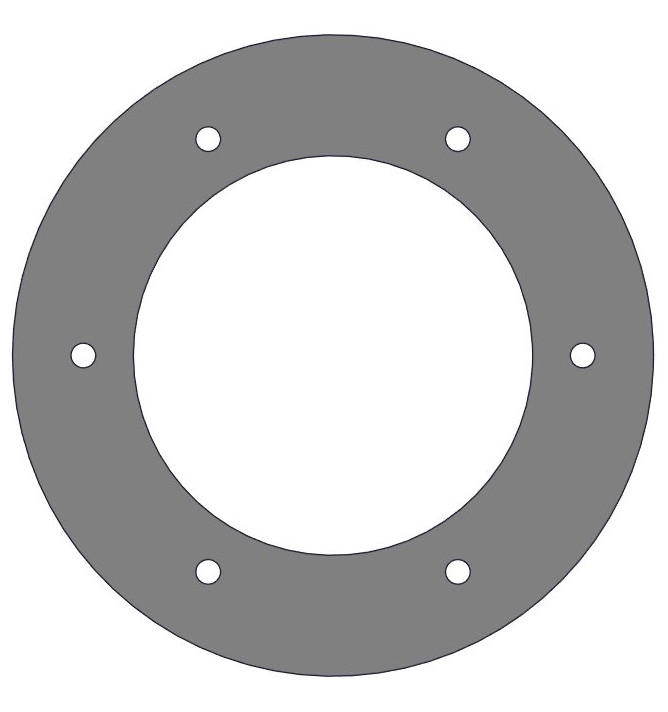
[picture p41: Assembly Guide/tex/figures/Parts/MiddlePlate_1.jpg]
		 &
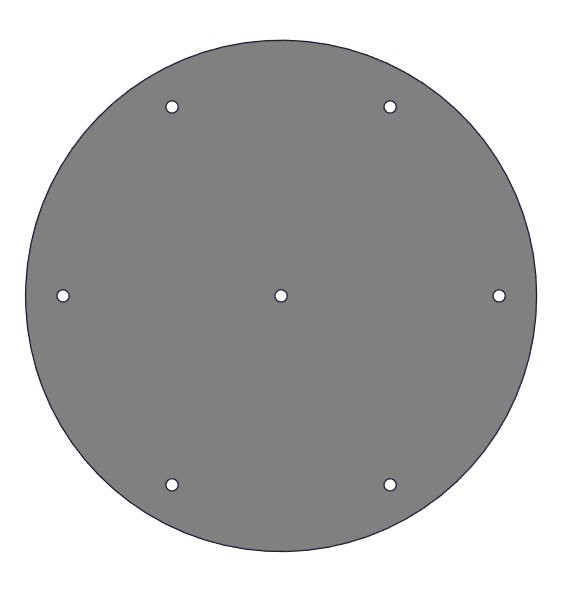
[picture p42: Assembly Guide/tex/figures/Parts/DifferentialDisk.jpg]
		 \\ 
		TopPlate & MiddlePlate &   DifferentialDisk \\
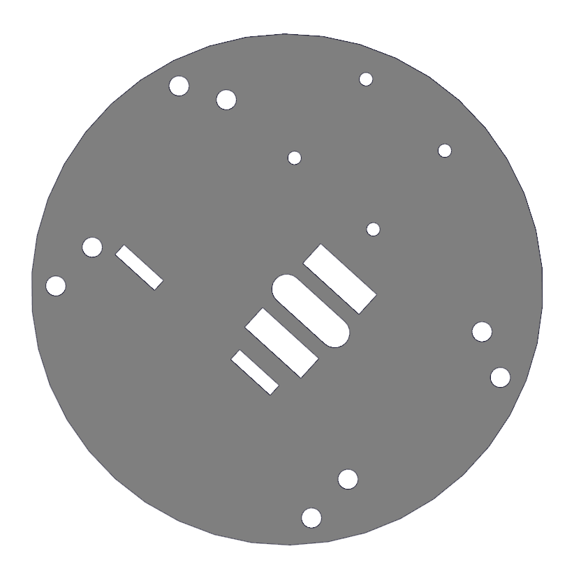
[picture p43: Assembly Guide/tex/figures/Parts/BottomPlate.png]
		 &
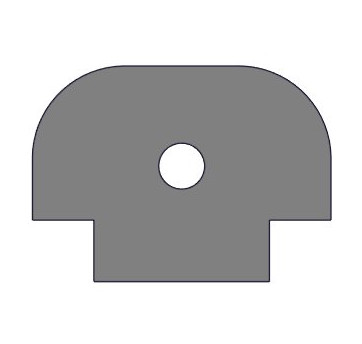
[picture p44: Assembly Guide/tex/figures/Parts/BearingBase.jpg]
		 &
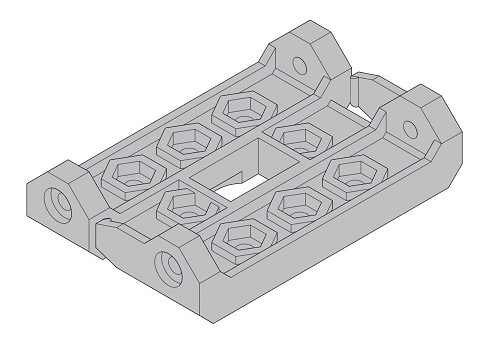
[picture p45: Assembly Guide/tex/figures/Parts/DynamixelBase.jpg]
		 \\
		BottomPlateAX12 & BearingBase &  AX12Base \\
    	\end{tabular}
};
\node[mytitle, right=10pt] at (box.north west) {Parts};
\end{tikzpicture}%
\end{center}

\newpage

\begin{center}
\begin{tikzpicture}
\node [mybox] (box){%
	\begin{tabular}{ c c c }
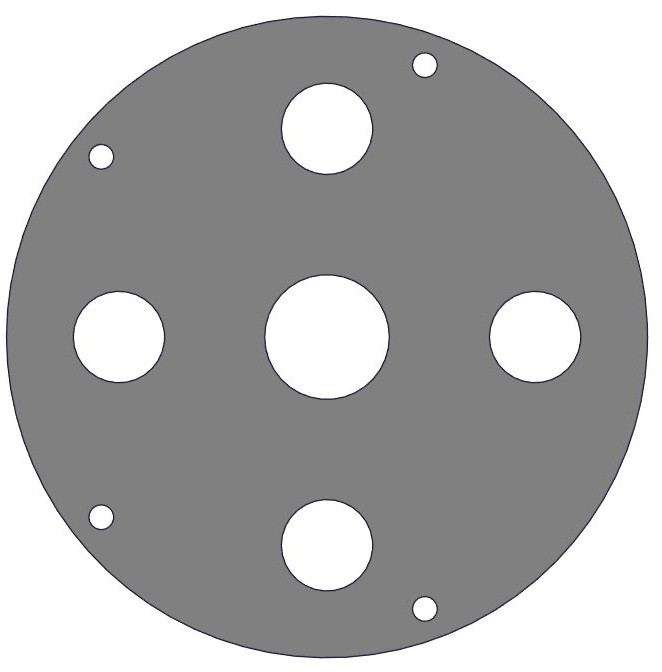
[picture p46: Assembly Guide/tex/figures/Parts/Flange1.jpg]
		 &
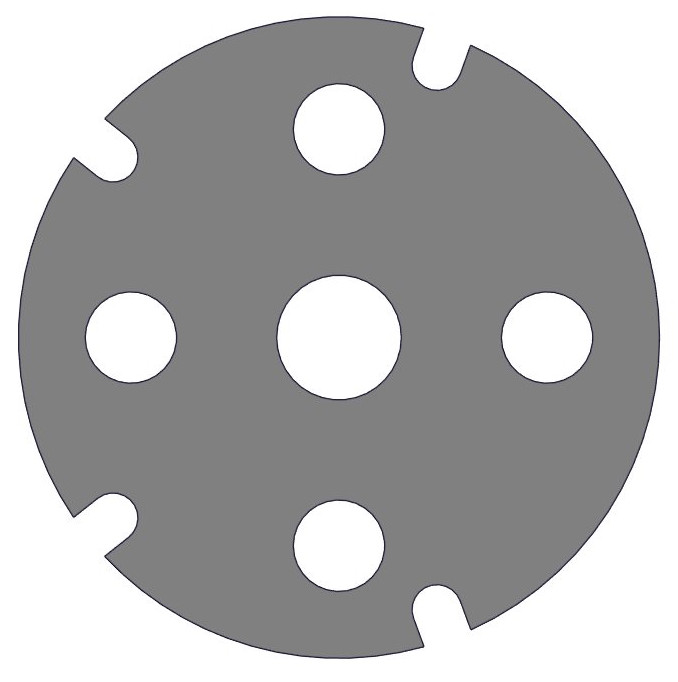
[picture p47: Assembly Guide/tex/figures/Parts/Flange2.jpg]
		 & 
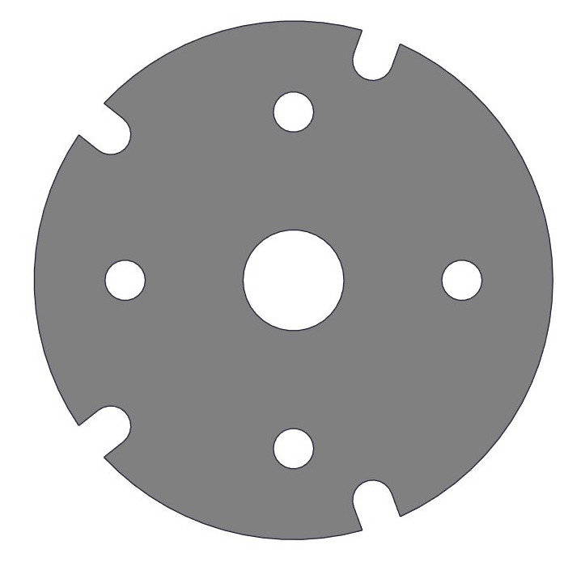
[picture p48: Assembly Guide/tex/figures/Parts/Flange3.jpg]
		 \\
		flangeAX12 \#1 & flangeAX12 \#2 &  flangeAX12 \#3\\ \\
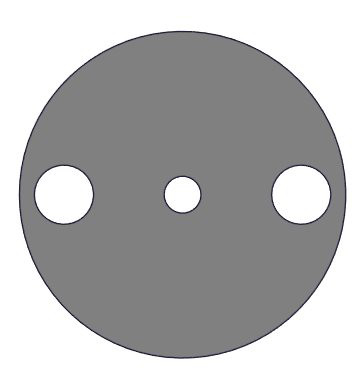
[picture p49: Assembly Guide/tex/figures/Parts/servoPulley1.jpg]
		 &
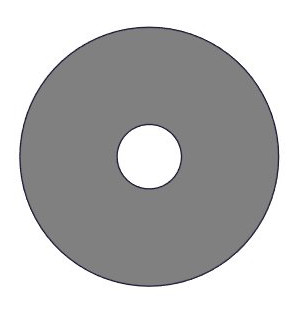
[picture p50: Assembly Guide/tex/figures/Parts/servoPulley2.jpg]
		 &
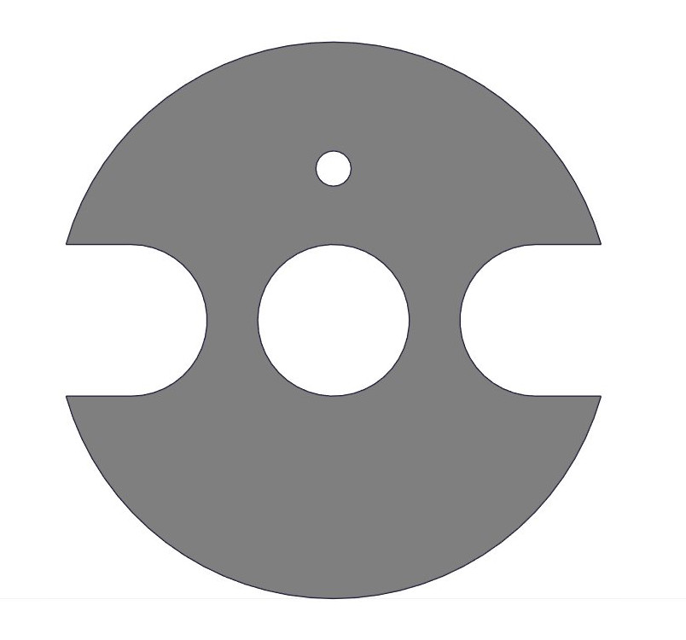
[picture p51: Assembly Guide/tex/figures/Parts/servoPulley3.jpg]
		 \\
		servoPulleyAX12 \#1 & servoPulleyAX12 \#2 & servoPulleyAX12 \#3 \\ \\
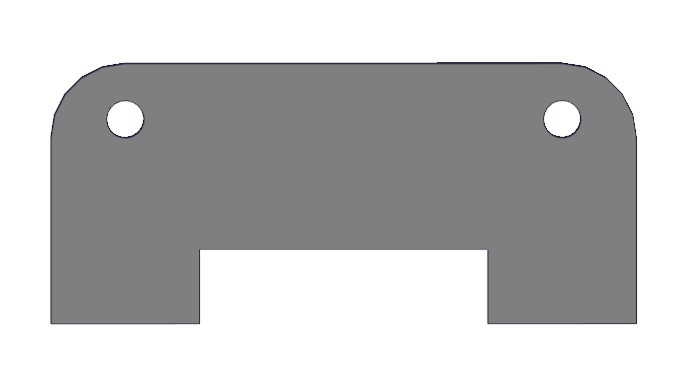
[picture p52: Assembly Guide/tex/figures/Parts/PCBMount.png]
		 &		
		 &
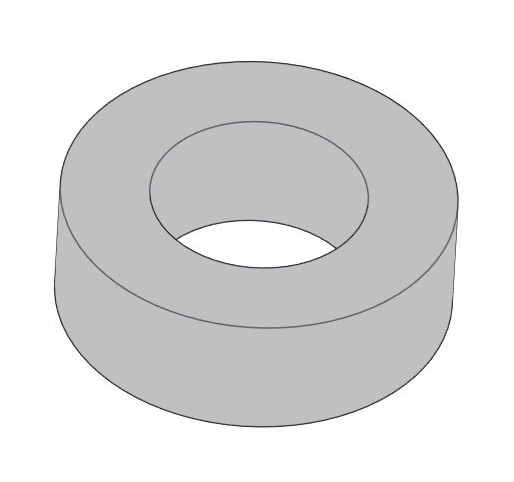
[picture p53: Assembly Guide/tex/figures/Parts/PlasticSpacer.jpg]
		 \\
 		PCBMount & pulley & PlasticSpacer \\ \\
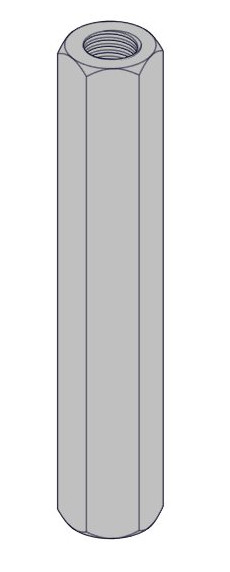
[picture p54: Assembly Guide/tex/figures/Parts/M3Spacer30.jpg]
		 &
		 &
		 \\
		M3Spacer30, M3Spacer25 & M3Spacer10 &  M3ThreadedRod \\ \\
		 &
		 &
		 \\
		M3x10, M3x20 & M3Washer & M3Nut \\ \\
		 &		
		 \\
		M2x6, M2x8 & M2Nut\\ \\
    	\end{tabular}
};
\end{tikzpicture}%
\end{center}

\newpage

\subsection{Robot Hand Base for Standard Servo}

\begin{table}[h!]
\centering
\scalebox{0.8}{
	\begin{tabular}{ | l | l | l |}
	\hline
 	\multicolumn{3}{|c|}{{\bf{Robot Hand Base for Standard Servo}}} \\
	\hline
	{\bf{Part Name}} & {\bf{Qty}} & {\bf{Description}}\\ \hline
    	TopPlate & 2 & Acrylic Part of Robot Hand Base  \\ \hline
    	MiddlePlate & 1 & Acrylic Part of Robot Hand Base\\ \hline
    	DifferentialDisk & 2 & Acrylic Part of  Differential Mechanism \\ \hline
    	BottomPlateStdServo & 2 & Acrylic Part of Robot Hand Base \\ \hline
    	BearingBase & 4 & Acrylic Part of Robot Hand Base \\ \hline
    	stdServoBase & 6 & Acrylic Part of Actuator Base \\ \hline
    	flangeStdServo \#1 & 1 & Acrylic Part of Flange \\ \hline
    	flangeStdServo \#2 & 1 & Acrylic Part of Flange \\ \hline
    	flangeStdServo \#3 & 1 & Acrylic Part of Flange \\ \hline
    	servoPulleyStd \#1 & 1 & Acrylic Part of Actuator Pulley \\ \hline    	
    	servoPulleyStd \#2 & 1 & Acrylic Part of Actuator Pulley \\ \hline
    	servoPulleyStd \#3 & 1 & Acrylic Part of Actuator Pulley \\ \hline
    	PCBMount & 1 & Acrylic Part for PCB \\ \hline    	    	    	    	
	Dyneema & 1 & Tendon Routing [D:0.4mm, Strength:41.5kg] \\ \hline
	Rubber Foam Tape & 1 & [Width:10mm, Thickness:4mm] \\ \hline
	Anti-Slip Tape & 1 & 3M Gripping Material [Width:25mm] \\ \hline
    	Hitec HS-311 & 1 &  Actuator\\ \hline
    	pulley & 1 & V-Groove Sealed Ball Bearing [d:3mm, D:12mm, B:4mm, Deepness:1.2mm] \\ \hline
    	PlasticSpacer & 2 & Fastener [d:3.1mm, D:6mm, L:2mm] \\ \hline
    	M3Spacer30 & 8 & Fastener, Spacer M3 [L:30mm] \\ \hline
    	M3Spacer25 & 4 & Fastener, Spacer M3 [L:25mm] \\ \hline
    	M3Spacer10 & 4 & Fastener, Spacer M3 [L:10mm] \\ \hline
	M3ThreadedRod & 4 & Fastener, M3 Threaded Rod [L:20mm]  \\ \hline	
    	M3x10 & 16 & Fastener, M3 [L:10mm] \\ \hline
    	M3x12 & 6 & Fastener, M3 [L:10mm] \\ \hline
    	M3x20 & 1 & Fastener, M3 [L:20mm] \\ \hline
    	M3Nut &  7 & Fastener, M3 Hex Nut \\ \hline
    	M3Washer &  18 & Fastener, M3 [D:7.5mm, L:0.5mm] \\ \hline
    	\end{tabular}
}
\end{table}

\vspace{0.2cm}

\begin{center}
\begin{tikzpicture}
\node [mybox] (box){%
	\begin{tabular}{ c c c }
		 &
		 & 
		 \\
		TopPlate & MiddlePlate & DifferentialDisk \\ \\
		 &
		 &
		 \\
		BottomPlate & BearingBase & stdServoBase \\
    	\end{tabular}
};
\node[mytitle, right=10pt] at (box.north west) {Parts};
\end{tikzpicture}%
\end{center}

\newpage

\begin{center}
\begin{tikzpicture}
\node [mybox] (box){%
	\begin{tabular}{ c c c }
		 &
		 & 
		 \\
		flangeStdServo \#1 & flangeStdServo \#2 &  flangeStdServo \#3\\ \\
		 &
		 &
		 \\
		servoPulleyStd \#1 & servoPulleyStd \#2 & servoPulleyStd \#3\\ \\
		 &		
		 &
		 \\
		PCBMount & pulley & PlasticSpacer \\ \\
		 &
		 &
		 \\
		 M3Spacer25, M3Spacer30 & M3Spacer10 & M3ThreadedRod \\ \\
		 &
		 &
		 \\
		M3x10, M3x12, M3x20 & M3Nut &  M3Washer\\ \\
    	\end{tabular}
};
\end{tikzpicture}%
\end{center}

\newpage

\subsection{3D Printer Parts}

The proposed robot hands can also be created with other materials like ABS, using 3D printing. The STL files in the CAD directory, are 
appropriate to be used with a 3D printer. The following table contains the required parts, as well as the names of the standard parts that they replace. 

\vspace{0.2cm}

\begin{table}[h!]
\centering
\scalebox{0.8}{
	\begin{tabular}{ | l | l |}
	\hline
 	\multicolumn{2}{|c|}{{\bf{3D Printer Parts}}} \\
	\hline
	{\bf{Part Name}} & {\bf{Replacing Parts}}\\ \hline
	FingerBase & FingerBase1, FingerBase2, FingerBase3, FingerMCP, TubePlateMCP parts  \\ \hline
    	FingerPIP & FingerPIP, TubePlate parts\\ \hline
    	FingerDIP & FingerDIP, TubePlate parts\\ \hline
    	TopPlate & TopPlate parts  \\ \hline
    	MiddlePlate & MiddlePlate part\\ \hline
    	DifferentialDisk & DifferentialDisk parts  \\ \hline
    	BottomPlateStdServo & BottomPlateStdServo, BearingBase parts \\ \hline
    	stdServoBase &  stdServoBase parts\\ \hline
	FlangeStdServo & flangeStdServo \#1, flangeStdServo \#2, flangeStdServo \#3 parts \\ \hline
    	BottomPlateAX12 & BottomPlateAX12,  BearingBase parts \\ \hline
    	FlangeAX12 & flangeAX12 \#1, flangeAX12 \#2, flangeAX12 \#3 parts \\ \hline
    	servoPulleyStd \#1-2 & servoPulleyStd \#1, servoPulleyStd \#2 parts\\ \hline    	
    	servoPulleyStd \#3 & servoPulleyStd \#3 part \\ \hline
    	servoPulleyAX12 \#1-2 & servoPulleyAX12 \#1, servoPulleyAX12 \#2 parts  \\ \hline    	
    	servoPulleyAX12 \#3 & servoPulleyAX12 \#3 parts  \\ \hline
    	PCBMount & PCBMount part  \\ \hline
    	\end{tabular}
}
\end{table}

\vspace{0.2cm}

\begin{center}
\begin{tikzpicture}
\node [mybox] (box){%
	\begin{tabular}{ c c c }
		 &
		 & 
		 \\
		FingerBase & FingerPIP & FingerDIP \\ \\
		 &
		 &
		 \\
		TopPlate & MiddlePlate & DifferentialDisk \\ \\
		 &
		 &
		 \\
		BottomPlateStdServo & stdServoBase & FlangeStdServo\\
    	\end{tabular}
};
\node[mytitle, right=10pt] at (box.north west) {3D Printer Parts};
\end{tikzpicture}%
\end{center}

\newpage

\begin{center}
\begin{tikzpicture}
\node [mybox] (box){%
	\begin{tabular}{ c c c }
		 &
		 &
		 \\
		BottomPlateAX12 & FlangeAX12 & servoPulleyStd \#1-2 \\ \\
		 &
		 &
		 \\
		servoPulleyStd \#3  & servoPulleyAX12 \#1-2  & servoPulleyAX12 \#3 \\
		 & & \\
		PCBMount & &\\
    	\end{tabular}
};
\end{tikzpicture}%
\end{center}

\vspace{1cm}

In order to print the required parts we use the \href{https://download.lulzbot.com/AO-100/documentation/LulzBot-AO-100-brochure.pdf}{LulzBot AO-100 Desktop 3D Printer}. The Slic3r (a G-code generator) printer settings are shown in the following table. The settings are also containted in a file named RobotHand.ini. 

\vspace{1cm}

\begin{table}[h!]
\centering
\scalebox{1}{
	\begin{tabular}{ | l | l |}
	\hline
 	\multicolumn{2}{|c|}{{\bf{3D Printer Settings}}} \\ \hline
	{\bf{Parameter}} & {\bf{Value}} \\ \hline
	Layer Height & 0.4022 \\ \hline   
	First Layer Height & 100\% \\ \hline   
	Solid Layers, Top & 3 \\ \hline
	Solid Layers, Bottom & 3 \\ \hline
	Infill, Fill Density & 40\% \\ \hline
	Infill, Fill Pattern & Honeycomb \\ \hline
	Infill, Top/Bottom Fill Pattern & Rectilinear \\ \hline
	Brim, Brim Width & 2 mm \\ \hline
	Support Material, Pattern & Pillars \\ \hline
	Support Material, Pattern Spacing & 2.5mm \\ \hline
	Support Material, Pattern Angle & 0 deg \\ \hline
	Support Material, Interface Layers & 3 layers \\ \hline
	Support Material, Interface Pattern Spacing & 0mm \\ \hline
    	\end{tabular}
}
\end{table}

\newpage

\subsection{Before Building}

Before starting the construction of the robot hand you must prepare the parts and pay attention to the steps provided below: \\  \\
$\bullet$ Smooth the acrylic parts with sandpaper. \\ \\
$\bullet$ Treat the ABS parts with acetone (more information: \href{http://blog.reprap.org/2013/02/vapor-treating-abs-rp-parts.html}{RepRap: Blog}).\\ \\
$\bullet$ Cut the cotton swabs, to the appropriate size (following the parts reference dimensions). \\ \\
$\bullet$ Cut the silicone sheets, to the appropriate size (following the parts reference dimensions). \\ \\
$\bullet$ Group the parts according to the parts reference. \\ \\
$\bullet$ Pay always attention to the details having the following icon \Circled{!}.\\ \\
$\bullet$ Please note that the provided models do not have the actual size of the parts.\\ \\

\begin{center}
\begin{tikzpicture}
\node [mybox] (box){%
        \begin{tabular}{ c }
	 \\
        Cutting the silicone sheets with a cutter and a ruler.
	\end{tabular}
};
\end{tikzpicture}%
\end{center}

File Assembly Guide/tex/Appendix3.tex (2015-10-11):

\section{Robot Finger}

\subsection{Prepare Parts for the Robot Finger}

\begin{table}[ht!]
  	\begin{minipage}[b]{0.50\linewidth}\centering
	\scalebox{0.97}{
	\begin{tabular}{ | c | c |}
		\hline
		{\bf{Part}} & {\bf{Qty}}\\ \hline
    		FingerBase1 & 8  \\ \hline
    		FingerBase2 & 4  \\ \hline
    		FingerBase3 & 4  \\ \hline
    		FingerMCP & 4  \\ \hline
    		TubePlateMCP & 8  \\ \hline
		FingerPIP& 4 \\ \hline
		FingerDIP & 4 \\ \hline
		Tubeplate & 12 \\ \hline
    		tubeMCP & 8  \\ \hline
    		tubePIP & 8  \\ \hline
    		tubeDIP & 8  \\ \hline
		M3x12 & 4 \\ \hline
		M3Washer & 16 \\ \hline
		M3Nut & 4 \\ \hline
		pulley & 4 \\ \hline
    	\end{tabular}
	}
	\end{minipage}
	\hspace{0.5cm}	
	\begin{minipage}[b]{0.50\linewidth}\centering
	\scalebox{1}{
	\begin{tabular}{ | c |}
		\hline
 		\multicolumn{1}{|c|}{\bf{Tools}} \\
		\hline
		Acrylic Glue \\ \hline
		Super Glue \\ \hline
		Allen Wrench 2.5mm\\ \hline
		Open-End Wrench \\ \hline
    	\end{tabular}
	}
  	\end{minipage}
\end{table}

\vspace{0.2cm}

\begin{center}
\begin{tikzpicture}
\node [mybox] (box){%
  	\begin{minipage}[b]{0.50\linewidth}\centering
	\begin{tabular}{ c }
		
    	\end{tabular}
	\end{minipage}
	\hspace{0.5cm}	
	\begin{minipage}[b]{0.50\linewidth}
	\begin{tabular}{ l }
		     \Circled{1} Glue FingerBase2 and FingerBase3 together \\ using acrylic glue. \\
		     \Circled{2} Glue FingerBase1 and FingerBase2-3 together \\ using acrylic glue. \\
		     \Circled{3} Continue as you see in the picture. \\
		     \Circled{!} Pay attention not to forget the M3 washers.
    	\end{tabular}
  	\end{minipage}
};
\node[mytitle, right=10pt] at (box.north west) {6.1.1};
\end{tikzpicture}%
\end{center}

\newpage

\begin{center}
\begin{tikzpicture}
\node [mybox] (box){%
  	\begin{minipage}[b]{0.50\linewidth}\centering
	\begin{tabular}{ c }
           	
    	\end{tabular}
	\end{minipage}
	\hspace{0.5cm}	
	\begin{minipage}[b]{0.50\linewidth}
	\begin{tabular}{ l }
		\Circled{1} Attach FingerBase1 to the previous part.\\  
		\Circled{2} Glue the previous part and FingerBase1 \\ together using acrylic glue. \\
		\Circled{3} Screw the M3Nut to the M3x12 screw.\\
		\Circled{!}  M3 washers must be in the right position. \\  
		\Circled{!}  Tighten the screw until the pulley\\ can freely move. 
    	\end{tabular}
  	\end{minipage}
};
\node[mytitle, right=10pt] at (box.north west) {6.1.2};
\end{tikzpicture}%
\end{center}

\vspace{0.2cm}

\begin{center}
\begin{tikzpicture}
\node [mybox] (box){%
  	\begin{minipage}[b]{0.50\linewidth}\centering
	\begin{tabular}{ l }
		\Circled{1} Glue FingerMCP and TubePlateMCP parts \\ together, using acrylic glue. \\
    	\end{tabular}
	\end{minipage}
	\hspace{0.5cm}	
	\begin{minipage}[b]{0.50\linewidth}
	\begin{tabular}{ c }
		
    	\end{tabular}
  	\end{minipage}
};
\node[mytitle, right=10pt] at (box.north west) {6.1.3};
\end{tikzpicture}%
\end{center}

\vspace{0.2cm}

\begin{center}
\begin{tikzpicture}
\node [mybox] (box){%
  	\begin{minipage}[b]{0.50\linewidth}\centering
	\begin{tabular}{ c }
		
    	\end{tabular}
	\end{minipage}
	\hspace{0.5cm}	
	\begin{minipage}[b]{0.50\linewidth}
	\begin{tabular}{ l }
		\Circled{1} Attach the FingerMCP part\\ to the FingerBase1 slots. \\ 
		\Circled{!} The FingerMCP part must fit\\ into the FingerBase1 slots. \\
		\Circled{2} Glue the two parts together\\ with acrylic glue.
    	\end{tabular}
  	\end{minipage}
};
\node[mytitle, right=10pt] at (box.north west) {6.1.4};
\end{tikzpicture}%
\end{center}

\newpage

\begin{center}
\begin{tikzpicture}
\node [mybox] (box){%
  	\begin{minipage}[b]{0.50\linewidth}\centering
	\begin{tabular}{ l }
		\Circled{1} Insert the low friction tubes to the \\ tube plates, as you see in the picture. \\
		\Circled{2} Glue the edges of the tubes to the \\ tube plate, using super glue. 
    	\end{tabular}
	\end{minipage}
	\hspace{0.5cm}	
	\begin{minipage}[b]{0.50\linewidth}
	\begin{tabular}{ l }
		
    	\end{tabular}
  	\end{minipage}
};
\node[mytitle, right=10pt] at (box.north west) {6.1.5};
\end{tikzpicture}%
\end{center}

\vspace{0.2cm}

\begin{center}
\begin{tikzpicture}
\node [mybox] (box){%
	\begin{tabular}{ c }
           	     
    	\end{tabular}
};
\node[mytitle, right=10pt] at (box.north west) {FingerBase part};
\end{tikzpicture}%
\end{center}

\vspace{0.2cm}

\begin{center}
\begin{tikzpicture}
\node [mybox] (box){%
  	\begin{minipage}[b]{0.50\linewidth}\centering
	\begin{tabular}{ l }
		\Circled{1} Glue FingerPIP and TubePlate together,\\ using acrylic glue. \\
    	\end{tabular}
	\end{minipage}
	\hspace{0.5cm}	
	\begin{minipage}[b]{0.50\linewidth}
	\begin{tabular}{ c }
		
    	\end{tabular}
  	\end{minipage}
};
\node[mytitle, right=10pt] at (box.north west) {6.1.6};
\end{tikzpicture}%
\end{center}

\newpage

\begin{center}
\begin{tikzpicture}
\node [mybox] (box){%
  	\begin{minipage}[b]{0.50\linewidth}\centering
	\begin{tabular}{ l }
		\Circled{1} Insert the low friction tubes to the \\ tube plates, as you see in the picture. \\
		\Circled{2} Glue the edges of the tubes to the \\ tube plate, using super glue. 
    	\end{tabular}
	\end{minipage}
	\hspace{0.5cm}	
	\begin{minipage}[b]{0.50\linewidth}
	\begin{tabular}{ l }
		
    	\end{tabular}
  	\end{minipage}
};
\node[mytitle, right=10pt] at (box.north west) {6.1.7};
\end{tikzpicture}%
\end{center}

\vspace{0.2cm}

\begin{center}
\begin{tikzpicture}
\node [mybox] (box){%
  	\begin{minipage}[b]{0.50\linewidth}\centering
	\begin{tabular}{ c }
		
    	\end{tabular}
	\end{minipage}
	\hspace{0.5cm}	
	\begin{minipage}[b]{0.50\linewidth}
	\begin{tabular}{ l }
		\Circled{1} Glue FingerDIP and TubePlate together,\\ using acrylic glue. \\
    	\end{tabular}
  	\end{minipage}
};
\node[mytitle, right=10pt] at (box.north west) {6.1.8};
\end{tikzpicture}%
\end{center}

\vspace{0.2cm}

\begin{center}
\begin{tikzpicture}
\node [mybox] (box){%
  	\begin{minipage}[b]{0.50\linewidth}\centering
	\begin{tabular}{ l }
		\Circled{1} Insert the low friction tubes to the \\ tube plates, as you see in the picture. \\
		\Circled{2} Glue the edges of the tubes to the \\ tube plate, using super glue.
    	\end{tabular}
	\end{minipage}
	\hspace{0.5cm}	
	\begin{minipage}[b]{0.50\linewidth}
	\begin{tabular}{ l }
		
    	\end{tabular}
  	\end{minipage}
};
\node[mytitle, right=10pt] at (box.north west) {6.1.9};
\end{tikzpicture}%
\end{center}

\newpage

\begin{center}
\begin{tikzpicture}
\node [mybox] (box){%
  	\begin{minipage}[b]{0.50\linewidth}\centering
	\begin{tabular}{ c }
		
    	\end{tabular}
	\end{minipage}
	\hspace{0.5cm}	
	\begin{minipage}[b]{0.50\linewidth}
	\begin{tabular}{ c }
		
    	\end{tabular}
  	\end{minipage}
};
\node[mytitle, right=10pt] at (box.north west) {FingerPIP and FingerDIP parts};
\end{tikzpicture}%
\end{center}

\vspace{0.2cm}

\subsection{Stitching the Rigid Parts onto the Flexure Joints }
\begin{table}[ht!]
  	\begin{minipage}[b]{0.50\linewidth}\centering
	\scalebox{0.97}{
	\begin{tabular}{ | c | c |}
		\hline
		{\bf{Part}} & {\bf{Qty}}\\ \hline
    		FingerBase & 4  \\ \hline
    		FingerPIP & 4  \\ \hline
    		FingerDIP & 4  \\ \hline
    		Joint1 & 4  \\ \hline
    		Joint2 & 4  \\ \hline
    	\end{tabular}
	}
	\end{minipage}
	\hspace{0.5cm}	
	\begin{minipage}[b]{0.50\linewidth}\centering
	\scalebox{1}{
	\begin{tabular}{ | c |}
		\hline
 		\multicolumn{1}{|c|}{{\bf{Tools}}} \\
		\hline
		Long Darners \\ \hline
		Nylon Fishing Line \\ \hline
		Cutter \\ \hline
		Long-Nose Pliers with Side-Cutting \\ \hline
		Precision Ruler \\ \hline
		Scissors \\ \hline
    	\end{tabular}
	}
  	\end{minipage}

\end{table}

\vspace{0.2cm}

\begin{center}
	\begin{tabular}{ c c }
		 &
		
    	\end{tabular}
\end{center}

\vspace{0.5cm}	

In order to connect together the rigid parts that we assembled in the previous sections, we use silicone sheets as flexure joints. 
These silicone sheets can be stitched onto the rigid parts, following the pattern that you see in the picture.
This sewing pattern creates a rigid connection between the rigid part and the flexure joint. \\
We use nylon fishing line and long darners for sewing. In the picture, the red lines depict a fishing line
passing from both sides of the rigid part and the flexure joint, while the blue lines depict a fishing line that passes only from 
the lower side of the flexure joint. The same sewing pattern can be used for both fingerPIP and fingerDIP parts. The following steps explain exactly this process.
	
\newpage

\begin{center}
\begin{tikzpicture}
\node [mybox] (box){%
  	\begin{minipage}[b]{0.50\linewidth}\centering
	\begin{tabular}{ c }
		 
    	\end{tabular}
	\end{minipage}
	\hspace{0.5cm}	
	\begin{minipage}[b]{0.50\linewidth}
	\begin{tabular}{ l }
		\Circled{1} Cut a 450mm fishing line. \\
		\Circled{2} Insert the fishing line to the holes \\ of two long darners. \\
		\Circled{3} Insert from the outer holes of the \\ upper side of the fingerMCP part the two \\  long darners, as you see in the picture. \\
    	\end{tabular}
  	\end{minipage}
};
\node[mytitle, right=10pt] at (box.north west) {6.2.1};
\end{tikzpicture}%
\end{center}

\vspace{0.2cm}

\begin{center}
\begin{tikzpicture}
\node [mybox] (box){%
  	\begin{minipage}[b]{0.50\linewidth}\centering
	\begin{tabular}{ l }
		\Circled{1} Insert each of the darners, to the hole \\ of the other darner. \\
		\Circled{2} Repeat \Circled{1} 2 times. \\
		\Circled{!} The darners are now in the lower side of \\ the fingerMCP part.\\
		\Circled{3} Insert the darners to the inner holes \\ of the fingerMCP part. \\
    	\end{tabular}
	\end{minipage}
	\hspace{0.5cm}	
	\begin{minipage}[b]{0.50\linewidth}
	\begin{tabular}{ l }
		
    	\end{tabular}
  	\end{minipage}
};
\node[mytitle, right=10pt] at (box.north west) {6.2.2};
\end{tikzpicture}%
\end{center}

\vspace{0.2cm}

\begin{center}
\begin{tikzpicture}
\node [mybox] (box){%
  	\begin{minipage}[b]{0.50\linewidth}\centering
	\begin{tabular}{ c }
           	      
    	\end{tabular}
	\end{minipage}
	\hspace{0.5cm}	
	\begin{minipage}[b]{0.50\linewidth}
	\begin{tabular}{ l }
		\Circled{1} Insert each one of the darners to the hole \\ of the other darner.\\
		\Circled{2} Repeat \Circled{1} 3 times. \\
		\Circled{!} The darners are now in the lower side of \\ the fingerMCP part.
    	\end{tabular}
  	\end{minipage}
};
\node[mytitle, right=10pt] at (box.north west) {6.2.3};
\end{tikzpicture}%
\end{center}

\newpage

\begin{center}
\begin{tikzpicture}
\node [mybox] (box){%
  	\begin{minipage}[b]{0.50\linewidth}\centering
	\begin{tabular}{ l }
		\Circled{1} Remove the darners from the fishing line. \\
		\Circled{2} With the two ends of the fishing line do \\ multiple surgeon's knots.
    	\end{tabular}
	\end{minipage}
	\hspace{0.5cm}	
	\begin{minipage}[b]{0.50\linewidth}
	\begin{tabular}{ c }
		
    	\end{tabular}
  	\end{minipage}
};
\node[mytitle, right=10pt] at (box.north west) {6.2.4};
\end{tikzpicture}%
\end{center}

\vspace{0.2cm}

\begin{center}
\begin{tikzpicture}
\node [mybox] (box){%
  	\begin{minipage}[b]{0.50\linewidth}\centering
	\begin{tabular}{ c }
           	     
    	\end{tabular}
	\end{minipage}
	\hspace{0.5cm}	
	\begin{minipage}[b]{0.50\linewidth}
	\begin{tabular}{ l }
		\Circled{1} Use a ruler to measure 8mm from the edge \\ of the fingerMCP part and draw a line\\ with a pen.
    	\end{tabular}
  	\end{minipage}
};
\node[mytitle, right=10pt] at (box.north west) {6.2.5};
\end{tikzpicture}%
\end{center}

\vspace{0.2cm}

\begin{center}
\begin{tikzpicture}
\node [mybox] (box){%
  	\begin{minipage}[b]{0.50\linewidth}\centering
	\begin{tabular}{ l }
		\Circled{1} Cut a 450mm fishing line. \\
		\Circled{2} Insert the fishing line to the holes \\ of two long darners. \\
		\Circled{3} Center the fingerPIP part with the silicone part\\ and align it with the line from the previous step.\\
		\Circled{4} Insert from the outer holes of the lower side \\ of the fingerPIP part the two long darners, \\ as you see in the picture. \\
    	\end{tabular}
	\end{minipage}
	\hspace{0.5cm}	
	\begin{minipage}[b]{0.50\linewidth}
	\begin{tabular}{ c }
		 
    	\end{tabular}
  	\end{minipage}
};
\node[mytitle, right=10pt] at (box.north west) {6.2.6};
\end{tikzpicture}%
\end{center}

\newpage

\begin{center}
\begin{tikzpicture}
\node [mybox] (box){%
  	\begin{minipage}[b]{0.50\linewidth}\centering
	\begin{tabular}{ c }
		
    	\end{tabular}
	\end{minipage}
	\hspace{0.5cm}	
	\begin{minipage}[b]{0.50\linewidth}
	\begin{tabular}{ l }
		\Circled{1} Insert each one of the darners to the hole of \\ the other darner.\\
		\Circled{2} Repeat \Circled{1} for 3 times. \\
		\Circled{!} The darners are now in the lower side \\ of the fingerPIP part. 
    	\end{tabular}
  	\end{minipage}
};
\node[mytitle, right=10pt] at (box.north west) {6.2.7};
\end{tikzpicture}%
\end{center}

\vspace{0.2cm}

\begin{center}
\begin{tikzpicture}
\node [mybox] (box){%
  	\begin{minipage}[b]{0.50\linewidth}\centering
	\begin{tabular}{ l }
		\Circled{1} Insert the darners to the inner holes \\ of the fingerPIP part from the lower side.\\
		\Circled{2} Insert each one of the darners to the hole\\ of the other darner.\\
		\Circled{3} Repeat \Circled{2} 3 times.\\
		\Circled{!} The darners are now in the lower side of \\ the fingerPIP part. \\
		\Circled{4} Remove the darners from the fishing line. \\
		\Circled{5} With the two ends of the fishing line do \\ multiple surgeon's knots.\\
    	\end{tabular}
	\end{minipage}
	\hspace{0.5cm}	
	\begin{minipage}[b]{0.50\linewidth}
	\begin{tabular}{ c }
		
    	\end{tabular}
  	\end{minipage}
};
\node[mytitle, right=10pt] at (box.north west) {6.2.8};
\end{tikzpicture}%
\end{center}

\vspace{0.2cm}

\begin{center}
\begin{tikzpicture}
\node [mybox] (box){%
  	\begin{minipage}[b]{0.50\linewidth}\centering
	\begin{tabular}{ c }
		
    	\end{tabular}
	\end{minipage}
	\hspace{0.5cm}	
	\begin{minipage}[b]{0.50\linewidth}
	\begin{tabular}{ l }
		\Circled{1} Repeat the 6.2.6 - 6.2.8 steps for the\\ FingerDIP part. \\
		\Circled{!} Congratulations, now you have a robot finger!
    	\end{tabular}
  	\end{minipage}
};
\node[mytitle, right=10pt] at (box.north west) {Robot Finger};
\end{tikzpicture}%
\end{center}

\newpage

\subsection{Tendon Routing of the Robot Finger}
\begin{table}[ht!]
  	\begin{minipage}[b]{0.50\linewidth}\centering
	\scalebox{0.97}{
	\begin{tabular}{ | c | c |}
		\hline
		{\bf{Part}} & {\bf{Qty}}\\ \hline
    		Robot Finger & 4  \\ \hline
		Dyneema & -- \\ \hline

    	\end{tabular}
	}
	\end{minipage}
	\hspace{0.5cm}	
	\begin{minipage}[b]{0.50\linewidth}\centering
	\scalebox{1}{
	\begin{tabular}{ | c |}
		\hline
 		\multicolumn{1}{|c|}{{\bf{Tools}}} \\
		\hline
		Scissors \\ \hline
		Precision Ruler \\ \hline
    	\end{tabular}
	}
  	\end{minipage}

\end{table}

\vspace{0.2cm}

\begin{center}
\begin{tikzpicture}
\node [mybox] (box){%
  	\begin{minipage}[b]{0.50\linewidth}\centering
	\begin{tabular}{ c }
		
    	\end{tabular}
	\end{minipage}
	\hspace{0.5cm}	
	\begin{minipage}[b]{0.50\linewidth}
	\begin{tabular}{ l }
		\Circled{1} Cut 600mm of the Dyneema fishing line. \\
		\Circled{2} Insert the Dyneema into the low friction tubes\\ starting from the tubeMCP. \\
    	\end{tabular}
  	\end{minipage}
};
\node[mytitle, right=10pt] at (box.north west) {6.3.1};
\end{tikzpicture}%
\end{center}

\vspace{0.2cm}

\begin{center}
\begin{tikzpicture}
\node [mybox] (box){%
  	\begin{minipage}[b]{0.50\linewidth}\centering
	\begin{tabular}{ l }
		\Circled{!}  Now the two edges of the Dyneema are \\ at the end of the tubeMCP. \\
		\Circled{1} Use a M3 spacer of 10mm length as \\ depicted in the picture. \\
    	\end{tabular}
	\end{minipage}
	\hspace{0.5cm}	
	\begin{minipage}[b]{0.50\linewidth}
	\begin{tabular}{ l }
           	     
    	\end{tabular}
  	\end{minipage}
};
\node[mytitle, right=10pt] at (box.north west) {6.3.2};
\end{tikzpicture}%
\end{center}

\vspace{0.2cm}

\begin{center}
\begin{tikzpicture}
\node [mybox] (box){%
  	\begin{minipage}[b]{0.50\linewidth}\centering
	\begin{tabular}{ c }
           	     
    	\end{tabular}
	\end{minipage}
	\hspace{0.5cm}	
	\begin{minipage}[b]{0.50\linewidth}
	\begin{tabular}{ l }
		\Circled{1} With the two edges of the Dyneema do \\ multiple surgeon's knots. \\
    	\end{tabular}
  	\end{minipage}
};
\node[mytitle, right=10pt] at (box.north west) {6.3.3};
\end{tikzpicture}%
\end{center}

\newpage

\subsection{Install Soft Fingetips}

\begin{table}[ht!]
  	\begin{minipage}[b]{0.50\linewidth}\centering
	\scalebox{0.97}{
	\begin{tabular}{ | c | c |}
		\hline
		{\bf{Part}} & {\bf{Qty}}\\ \hline
    		Robot Finger &  4  \\ \hline
		Sponge Tape & -- \\ \hline
		Self-adhesive Tape & -- \\ \hline
		Anti-Slip Tape & -- \\ \hline
    	\end{tabular}
	}
	\end{minipage}
	\hspace{0.5cm}	
	\begin{minipage}[b]{0.50\linewidth}\centering
	\scalebox{1}{
	\begin{tabular}{ | c |}
		\hline
 		\multicolumn{1}{|c|}{{\bf{Tools}}} \\
		\hline
		Scissors \\ \hline
    	\end{tabular}
	}
  	\end{minipage}

\end{table}

\vspace{0.2cm}

\begin{center}
\begin{tikzpicture}
\node [mybox] (box){%
  	\begin{minipage}[b]{0.50\linewidth}\centering
	\begin{tabular}{ c }
		
    	\end{tabular}
	\end{minipage}
	\hspace{0.5cm}	
	\begin{minipage}[b]{0.50\linewidth}
	\begin{tabular}{ l }
		\Circled{1} Cut two pieces of 24mm sponge tape. \\
		\Circled{2} Set the two pieces onto the FingerPIP part. \\
    	\end{tabular}
  	\end{minipage}
};
\node[mytitle, right=10pt] at (box.north west) {6.4.1};
\end{tikzpicture}%
\end{center}

\vspace{0.2cm}

\begin{center}
\begin{tikzpicture}
\node [mybox] (box){%
  	\begin{minipage}[b]{0.50\linewidth}\centering
	\begin{tabular}{ l }
		\Circled{1} Cut a piece of 130mm self-adhesive tape. \\
		\Circled{2} Wrap the tape around the FingerPIP part. \\
    	\end{tabular}
	\end{minipage}
	\hspace{0.5cm}	
	\begin{minipage}[b]{0.50\linewidth}
	\begin{tabular}{ c }
		
    	\end{tabular}
  	\end{minipage}
};
\node[mytitle, right=10pt] at (box.north west) {6.4.2};
\end{tikzpicture}%
\end{center}

\vspace{0.2cm}

\begin{center}
\begin{tikzpicture}
\node [mybox] (box){%
  	\begin{minipage}[b]{0.50\linewidth}\centering
	\begin{tabular}{ c }
		
    	\end{tabular}
	\end{minipage}
	\hspace{0.5cm}	
	\begin{minipage}[b]{0.50\linewidth}
	\begin{tabular}{ l }
		\Circled{1} Cut two pieces of 32mm sponge tape. \\
		\Circled{2} Set the two pieces onto the FingerDIP part. \\
		\Circled{3} Cut a piece of 10mm sponge tape. \\
		\Circled{4} Set the sponge tape onto the empty space \\ of the FingerDIP part. \\
		\Circled{5} Cut two pieces of 40mm sponge tape and \\ set them onto the other side.
    	\end{tabular}
  	\end{minipage}
};
\node[mytitle, right=10pt] at (box.north west) {6.4.3};
\end{tikzpicture}%
\end{center}

\vspace{0.2cm}

\begin{center}
\begin{tikzpicture}
\node [mybox] (box){%
  	\begin{minipage}[b]{0.50\linewidth}\centering
	\begin{tabular}{ c }
		
    	\end{tabular}
	\end{minipage}
	\hspace{0.5cm}	
	\begin{minipage}[b]{0.50\linewidth}
	\begin{tabular}{ l }
		\Circled{1} Cut a piece of 200mm self-adhesive tape. \\
		\Circled{2} Wrap the tape around the FingerDIP part. \\
    	\end{tabular}
  	\end{minipage}
};
\node[mytitle, right=10pt] at (box.north west) {6.4.4};
\end{tikzpicture}%
\end{center}

\newpage

\begin{center}
\begin{tikzpicture}
\node [mybox] (box){%
  	\begin{minipage}[b]{0.50\linewidth}\centering
	\begin{tabular}{ l }
		\Circled{1} Cut a piece of 27mm anti-slip tape. \\
		\Circled{2} Attach the tape onto the FingerPIP part. \\
		\Circled{3} Cut a piece of 40mm anti-slip tape. \\
		\Circled{4} Attach the tape onto the FingerDIP part. \\
		\Circled{!} Cut the edges of the tape at the FingerDIP part. \\
    	\end{tabular}
	\end{minipage}
	\hspace{0.5cm}	
	\begin{minipage}[b]{0.50\linewidth}
	\begin{tabular}{ c }
		
    	\end{tabular}
  	\end{minipage}
};
\node[mytitle, right=10pt] at (box.north west) {6.4.5};
\end{tikzpicture}%
\end{center}

\vspace{0.5cm}

\subsection{Install Soft Pad to the Top Plate of the Robot Base}

\begin{table}[ht!]
  	\begin{minipage}[b]{0.50\linewidth}\centering
	\scalebox{0.97}{
	\begin{tabular}{ | c | c |}
		\hline
		{\bf{Part}} & {\bf{Qty}}\\ \hline
    		TopPlate & 2  \\ \hline
		Sponge Tape & -- \\ \hline
		Anti-Slip Tape & -- \\ \hline
    	\end{tabular}
	}
	\end{minipage}
	\hspace{0.5cm}	
	\begin{minipage}[b]{0.50\linewidth}\centering
	\scalebox{1}{
	\begin{tabular}{ | c |}
		\hline
 		\multicolumn{1}{|c|}{Tools} \\
		\hline
		Acrylic Glue \\ \hline
		Scissors \\ \hline
    	\end{tabular}
	}
  	\end{minipage}

\end{table}

\vspace{0.2cm}

\begin{center}
\begin{tikzpicture}
\node [mybox] (box){%
  	\begin{minipage}[b]{0.50\linewidth}\centering
	\begin{tabular}{ c }
		 
    	\end{tabular}
	\end{minipage}
	\hspace{0.5cm}	
	\begin{minipage}[b]{0.50\linewidth}
	\begin{tabular}{ l }
		\Circled{1} Glue the TopPlate parts. \\
		\Circled{!} Center the two parts as depicted.
    	\end{tabular}
  	\end{minipage}
};
\node[mytitle, right=10pt] at (box.north west) {6.5.1};
\end{tikzpicture}%
\end{center}

\vspace{0.2cm}

\begin{center}
\begin{tikzpicture}
\node [mybox] (box){%
  	\begin{minipage}[b]{0.50\linewidth}\centering
	\begin{tabular}{ l }
		\Circled{1} Cut three pieces of 25mm sponge tape. \\
		\Circled{2} Put the pieces of tape in the middle of \\ the TopPlate part. \\
    	\end{tabular}
	\end{minipage}
	\hspace{0.5cm}	
	\begin{minipage}[b]{0.50\linewidth}
	\begin{tabular}{ c }
		 
    	\end{tabular}
  	\end{minipage}
};
\node[mytitle, right=10pt] at (box.north west) {6.5.2};
\end{tikzpicture}%
\end{center}

\newpage

\begin{center}
\begin{tikzpicture}
\node [mybox] (box){%
  	\begin{minipage}[b]{0.50\linewidth}\centering
	\begin{tabular}{ c }
		 
    	\end{tabular}
	\end{minipage}
	\hspace{0.5cm}	
	\begin{minipage}[b]{0.50\linewidth}
	\begin{tabular}{ l }
		\Circled{1} Cut a piece of 32mm anti-slip tape. \\
		\Circled{2} Attach the tape pieces onto the sponge tape. \\
    	\end{tabular}
  	\end{minipage}
};
\node[mytitle, right=10pt] at (box.north west) {6.5.3};
\end{tikzpicture}%
\end{center}

\vspace{0.5cm}

\subsection{Install the Robot Fingers to the TopPlate}

\begin{table}[ht!]
  	\begin{minipage}[b]{0.50\linewidth}\centering
	\scalebox{0.97}{
	\begin{tabular}{ | c | c |}
		\hline
		{\bf{Part}} & {\bf{Qty}}\\ \hline
    		TopPlate & 1 \\ \hline
		Robot Finger & 4 \\ \hline
		M3x12 & 4 \\ \hline
		M3Washer & 4 \\ \hline
		M3Nut & 5 \\ \hline
    	\end{tabular}
	}
	\end{minipage}
	\hspace{0.5cm}	
	\begin{minipage}[b]{0.50\linewidth}\centering
	\scalebox{1}{
	\begin{tabular}{ | c |}
		\hline
 		\multicolumn{1}{|c|}{{\bf{Tools}}} \\
		\hline
		Allen Wrench 2.5mm \\ \hline
    	\end{tabular}
	}
  	\end{minipage}

\end{table}

\vspace{0.2cm}

\begin{center}
\begin{tikzpicture}
\node [mybox] (box){%
  	\begin{minipage}[b]{0.50\linewidth}\centering
	\begin{tabular}{ c }
		
    	\end{tabular}
	\end{minipage}
	\hspace{0.5cm}	
	\begin{minipage}[b]{0.50\linewidth}
	\begin{tabular}{ l }
		\Circled{1} Keep the TopPlate part and the robot finger.\\
		\Circled{2} Insert the M3Nut in the FingerBase part.\\
		\Circled{3} Insert the robot finger to the slot \\ of the TopPlate.\\
		\Circled{4} Center the M3Nut with the holes of \\ the FingerBase and the TopPlate parts.\\
		\Circled{5} Insert the M3x12 screw with the M3 washer \\ in the hole of the TopPlate.\\
		\Circled{6} Tighten the M3x12 screw. \\
		\Circled{7} Repeat the steps to install all the robot \\ fingers to the TopPlate.
    	\end{tabular}
  	\end{minipage}
};
\node[mytitle, right=10pt] at (box.north west) {6.6.1};
\end{tikzpicture}%
\end{center}

\newpage

\begin{center}
\begin{tikzpicture}
\node [mybox] (box){%
	\begin{tabular}{ c }
		
    	\end{tabular}
};
\node[mytitle, right=10pt] at (box.north west) {TopPlate with Robot Finger};
\end{tikzpicture}%
\end{center}

\vspace{0.1cm}

\begin{center}
\begin{tikzpicture}
\node [mybox] (box){%
  	\begin{minipage}[b]{0.50\linewidth}\centering
	\begin{tabular}{ l }
		\Circled{1} Cut 20mm of Dyneema fishing line.\\
		\Circled{2} Pass the Dyneema fishing line through\\ the FingerBase tendon loop or spacer. \\
                \Circled{!} Leave both edges of the Dyneema free!\\
		\Circled{3} Repeat the steps for all robot fingers. \\ 
    	\end{tabular}
	\end{minipage}
	\hspace{0.5cm}	
	\begin{minipage}[b]{0.50\linewidth}
	\begin{tabular}{ c }
		
    	\end{tabular}
  	\end{minipage}
};
\node[mytitle, right=10pt] at (box.north west) {6.6.2};
\end{tikzpicture}%
\end{center}

\vspace{0.1cm}

\begin{center}
\begin{tikzpicture}
\node [mybox] (box){%
  	\begin{minipage}[b]{0.50\linewidth}\centering
	\begin{tabular}{c }
		
    	\end{tabular}
	\end{minipage}
	\hspace{0.5cm}	
	\begin{minipage}[b]{0.50\linewidth}
	\begin{tabular}{ l }
		\Circled{1} Cut 400mm of Dyneema fishing line. \\
		\Circled{2} Pass the Dyneema from the hole of a M3 nut \\ and do a non-slip knot. \\
		\Circled{3} Insert the Dyneema into the centered hole \\ of the differential mechanism. \\
                \Circled{!} The nut will keep the Dyneema constrained \\ at the one side!
    	\end{tabular}
  	\end{minipage}
};
\node[mytitle, right=10pt] at (box.north west) {6.6.3};
\end{tikzpicture}%
\end{center}

\vspace{0.1cm}

\begin{center}
\begin{tikzpicture}
\node [mybox] (box){%
  	\begin{minipage}[b]{0.50\linewidth}\centering
	\begin{tabular}{ l }
		\Circled{1} Center the holes of the differential disk \\ with the TopPlate slots. \\ 
		\Circled{2} Insert one edge of the FingerBase Dyneema \\ into one of the holes of the differential. \\
		\Circled{3} With the two edges of the Dyneema do \\ multiple surgeon's knots. \\
		\Circled{4} Repeat the steps for all robot fingers. \\
    	\end{tabular}
	\end{minipage}
	\hspace{0.5cm}	
	\begin{minipage}[b]{0.50\linewidth}
	\begin{tabular}{ c }
		
    	\end{tabular}
  	\end{minipage}
};
\node[mytitle, right=10pt] at (box.north west) {6.6.4};
\end{tikzpicture}%
\end{center}

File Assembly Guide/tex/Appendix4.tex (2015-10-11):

\section{Robot Hand Base}

\subsection{Middle Plate}

\begin{table}[ht!]
  	\begin{minipage}[b]{0.50\linewidth}\centering
	\scalebox{0.97}{
	\begin{tabular}{ | c | c |}
		\hline
		{\bf{Part}} & {\bf{Qty}}\\ \hline
    		MiddlePlate & 1  \\ \hline
    		M3Spacer30 & 8  \\ \hline
		M3ThreadedRod & 4 \\ \hline
    	\end{tabular}
	}
	\end{minipage}
	\hspace{0.5cm}	
	\begin{minipage}[b]{0.50\linewidth}\centering
	\scalebox{1}{
	\begin{tabular}{ | c |}
		\hline
 		\multicolumn{1}{|c|}{{\bf{Tools}}} \\
		\hline
		Open-End Wrench \\ \hline
    	\end{tabular}
	}
  	\end{minipage}

\end{table}

\vspace{0.5cm}

\begin{center}
\begin{tikzpicture}
\node [mybox] (box){%
  	\begin{minipage}[b]{0.50\linewidth}\centering
	\begin{tabular}{ c }
		
    	\end{tabular}
	\end{minipage}
	\hspace{0.5cm}	
	\begin{minipage}[b]{0.50\linewidth}
	\begin{tabular}{ l }
		\Circled{1} Tighten the M3ThreadedRod until \\ the midway (12mm). \\
		\Circled{2} Continue as you see in the picture.
    	\end{tabular}
  	\end{minipage}
};
\node[mytitle, right=10pt] at (box.north west) {7.1.1};
\end{tikzpicture}%
\end{center}

\subsection{Bearing Base}

\begin{table}[ht!]
  	\begin{minipage}[b]{0.50\linewidth}\centering
	\scalebox{0.97}{
	\begin{tabular}{ | c | c |}
		\hline
		{\bf{Part}} & {\bf{Qty}}\\ \hline
    		BearingBase & 4  \\ \hline
		pulley & 1 \\ \hline
		M3x20 & 1 \\ \hline
		M3Washer & 3 \\ \hline
		PlasticSpacer & 2 \\ \hline
		M3Nut & 1 \\ \hline
    	\end{tabular}
	}
	\end{minipage}
	\hspace{0.5cm}	
	\begin{minipage}[b]{0.50\linewidth}\centering
	\scalebox{1}{
	\begin{tabular}{ | c |}
		\hline
 		\multicolumn{1}{|c|}{{\bf{Tools}}} \\
		\hline
		Open-End Wrench \\ \hline
		Acrylic Glue \\ \hline
		Allen Wrench \\ \hline
    	\end{tabular}
	}
  	\end{minipage}
\end{table}

\begin{center}
\begin{tikzpicture}
\node [mybox] (box){%
  	\begin{minipage}[b]{0.50\linewidth}\centering
	\begin{tabular}{ c }
           	      
    	\end{tabular}
	\end{minipage}
	\hspace{0.5cm}	
	\begin{minipage}[b]{0.50\linewidth}
	\begin{tabular}{ l }
		\Circled{1} Center the two BearingBase parts. \\
		\Circled{2} Glue the two BearingBase parts. \\
		\Circled{3} Repeat the same steps for the \\ second BearingBase. \\
    	\end{tabular}
  	\end{minipage}
};
\node[mytitle, right=10pt] at (box.north west) {7.2.1};
\end{tikzpicture}%
\end{center}

\newpage

\subsection{Bottom Plate with AX12 Servo}

\begin{table}[ht!]
  	\begin{minipage}[b]{0.50\linewidth}\centering
	\scalebox{0.97}{
	\begin{tabular}{ | c | c |}
		\hline
		{\bf{Part}} & {\bf{Qty}}\\ \hline
    		BearingBase & 4  \\ \hline
    		BottomPlateAX12 & 2  \\ \hline
                PCBMount & 1 \\ \hline
		AX12Base & 1 \\ \hline
		M2x8 & 4 \\ \hline
		M2Nut & 4 \\ \hline
    	\end{tabular}
	}
	\end{minipage}
	\hspace{0.5cm}	
	\begin{minipage}[b]{0.50\linewidth}\centering
	\scalebox{1}{
	\begin{tabular}{ | c |}
		\hline
 		\multicolumn{1}{|c|}{{\bf{Tools}}} \\
		\hline
		Open-End Wrench \\ \hline
		Acrylic Glue \\ \hline
		Allen Wrench \\ \hline
    	\end{tabular}
	}
  	\end{minipage}
\end{table}

\begin{center}
\begin{tikzpicture}
\node [mybox] (box){%
  	\begin{minipage}[b]{0.50\linewidth}\centering
	\begin{tabular}{ l }
		\Circled{1} Center the two BottomPlate parts. \\
		\Circled{2} Glue the two BottomPlate parts. \\
		\Circled{3} Glue the BearingBase to the \\ BottomPlateAX12 with acrylic glue. \\
                \Circled{4} Glue the PCBMount to the BottomPlateAX12. \\
    	\end{tabular}
	\end{minipage}
	\hspace{0.5cm}	
	\begin{minipage}[b]{0.50\linewidth}
	\begin{tabular}{ l }
 	 	 
    	\end{tabular}
  	\end{minipage}
};
\node[mytitle, right=10pt] at (box.north west) {7.3.1};
\end{tikzpicture}%
\end{center}

\newpage

\subsection{Bottom Plate with Standard Servo}

\begin{table}[ht!]
  	\begin{minipage}[b]{0.50\linewidth}\centering
	\scalebox{0.97}{
	\begin{tabular}{ | c | c |}
		\hline
		{\bf{Part}} & {\bf{Qty}}\\ \hline
    		BottomPlateStdServo & 2  \\ \hline
    		BearingBase & 1  \\ \hline
		stdServoBase & 6 \\ \hline
                PCBMount & 1 \\ \hline
		M3x12 & 2 \\ \hline
		M3Washer & 2 \\ \hline
		M3Nut & 2 \\ \hline
    	\end{tabular}
	}
	\end{minipage}
	\hspace{0.5cm}	
	\begin{minipage}[b]{0.50\linewidth}\centering
	\scalebox{1}{
	\begin{tabular}{ | c |}
		\hline
 		\multicolumn{1}{|c|}{{\bf{Tools}}} \\
		\hline
		Allen Wrench \\ \hline
		Acrylic Glue \\ \hline
    	\end{tabular}
	}
  	\end{minipage}
\end{table}

\vspace{0.2cm}

\begin{center}
\begin{tikzpicture}
\node [mybox] (box){%
  	\begin{minipage}[b]{0.50\linewidth}\centering
	\begin{tabular}{ c }
		
    	\end{tabular}
	\end{minipage}
	\hspace{0.5cm}	
	\begin{minipage}[b]{0.50\linewidth}
	\begin{tabular}{ l }
		\Circled{1} Center the two stdServoBase parts. \\
		\Circled{2} Glue the two stdServoBase parts. \\
		\Circled{3} Center the third stdServoBase part\\ with the other two. \\
		\Circled{4} Glue the third stdServoBase part\\ with the other two. \\
    	\end{tabular}
  	\end{minipage}
};
\node[mytitle, right=10pt] at (box.north west) {7.4.1};
\end{tikzpicture}%
\end{center}

\vspace{0.2cm}

\begin{center}
\begin{tikzpicture}
\node [mybox] (box){%
  	\begin{minipage}[b]{0.50\linewidth}\centering
	\begin{tabular}{ l }
		\Circled{1} Center the BottomPlateStdServo \\ as you see in the picture. \\
		\Circled{2} Glue the two parts with acrylic glue. \\
		\Circled{3} Center the BearingBase with the \\ BottomPlateStdServo as you see in the picture. \\
		\Circled{4} Glue the two parts with acrylic glue. \\
                \Circled{5} Glue the PCBMount to the\\ BottomPlateStdServo. \\
		\Circled{6} Continue as you see in the picture.
    	\end{tabular}
	\end{minipage}
	\hspace{0.5cm}	
	\begin{minipage}[b]{0.50\linewidth}
	\begin{tabular}{ c }
		
    	\end{tabular}
  	\end{minipage}
};
\node[mytitle, right=10pt] at (box.north west) {7.4.2};
\end{tikzpicture}%
\end{center}

\newpage

\subsection{Robot Base with AX12 Servo}

\begin{table}[ht!]
  	\begin{minipage}[b]{0.50\linewidth}\centering
	\scalebox{0.97}{
	\begin{tabular}{ | c | c |}
		\hline
		{\bf{Part}} & {\bf{Qty}}\\ \hline
		MiddlePlate& 1 \\ \hline
		BottomPlateAX12 & 1 \\ \hline
		FingersTopPlate & 1 \\ \hline
		M3x10 & 8 \\ \hline
		M3Washer & 8 \\ \hline
    	\end{tabular}
	}
	\end{minipage}
	\hspace{0.5cm}	
	\begin{minipage}[b]{0.50\linewidth}\centering
	\scalebox{1}{
	\begin{tabular}{ | c |}
		\hline
 		\multicolumn{1}{|c|}{{\bf{Tools}}} \\
		\hline
		Open-End Wrench \\ \hline
		Allen Wrench\\ \hline
    	\end{tabular}
	}
  	\end{minipage}
\end{table}

\vspace{0.5cm}

\begin{center}
\begin{tikzpicture}
\node [mybox] (box){%
	
};
\node[mytitle, right=10pt] at (box.north west) {7.5.1};
\end{tikzpicture}%
\end{center}

\newpage

\subsection{Robot Base with Standard Servo}

\begin{table}[ht!]
  	\begin{minipage}[b]{0.50\linewidth}\centering
	\scalebox{0.97}{
	\begin{tabular}{ | c | c |}
		\hline
		{\bf{Part}} & {\bf{Qty}}\\ \hline
		MiddlePlate & 1 \\ \hline
		BottomPlateStdServo & 1 \\ \hline
		FingersTopPlate& 1 \\ \hline
		M3x10 & 8 \\ \hline
		M3Washer & 8 \\ \hline
    	\end{tabular}
	}
	\end{minipage}
	\hspace{0.5cm}	
	\begin{minipage}[b]{0.50\linewidth}\centering
	\scalebox{1}{
	\begin{tabular}{ | c |}
		\hline
 		\multicolumn{1}{|c|}{{\bf{Tools}}} \\
		\hline
		Open-End Wrench \\ \hline
		Allen Wrench\\ \hline
    	\end{tabular}
	}
  	\end{minipage}
\end{table}

\vspace{0.5cm}

\begin{center}
\begin{tikzpicture}
\node [mybox] (box){%
	
};
\node[mytitle, right=10pt] at (box.north west) {7.6.1};
\end{tikzpicture}%
\end{center}

\newpage

\subsection{AX12 Servo}

\begin{table}[ht!]
  	\begin{minipage}[b]{0.50\linewidth}\centering
	\scalebox{0.97}{
	\begin{tabular}{ | c | c |}
		\hline
		{\bf{Part}} & {\bf{Qty}}\\ \hline
		AX12Base & 1\\ \hline
		servoPulleyAX12 \#1 & 1 \\ \hline
		servoPulleyAX12 \#2 & 1 \\ \hline
		servoPulleyAX12 \#3 & 1 \\ \hline
		AX12 Servo& 1 \\ \hline
		M2x8 & 4 \\ \hline
		M2Nut & 4 \\ \hline
		M2x6 & 2 \\ \hline
		M2.5x15 & 1  \\ \hline
    	\end{tabular}
	}
	\end{minipage}
	\hspace{0.5cm}	
	\begin{minipage}[b]{0.50\linewidth}\centering
	\scalebox{1}{
	\begin{tabular}{ | c |}
		\hline
 		\multicolumn{1}{|c|}{{\bf{Tools}}} \\
		\hline
		Acrylic Glue \\ \hline
		Allen Wrench\\ \hline
    	\end{tabular}
	}
  	\end{minipage}
\end{table}

\vspace{0.2cm}

\begin{center}
\begin{tikzpicture}
\node [mybox] (box){%
  	\begin{minipage}[b]{0.50\linewidth}\centering
	\begin{tabular}{ c }
		
    	\end{tabular}
	\end{minipage}
	\hspace{0.5cm}	
	\begin{minipage}[b]{0.50\linewidth}
	\begin{tabular}{ l }
		\Circled{1} Center the servoPulleyAX12 parts \#1,2.\\
		\Circled{2} Glue the two parts with acrylic glue. \\
		\Circled{3} Center the servoPulleyAX12 parts \#1-2,3. \\
		\Circled{4} Glue the two parts with acrylic glue. \\
		\Circled{!} Press all the parts together\\ to achieve better gluing. \\
    	\end{tabular}
  	\end{minipage}
};
\node[mytitle, right=10pt] at (box.north west) {7.7.1};
\end{tikzpicture}%
\end{center}

\vspace{0.2cm}

\begin{center}
\begin{tikzpicture}
\node [mybox] (box){%
  	\begin{minipage}[b]{0.50\linewidth}\centering
	\begin{tabular}{ l }
		\Circled{1} Insert a Dyneema edge in the anchor hole. \\
		\Circled{2} With the edge of the Dyneema and the M3Nut \\ do multiple surgeon's knots. \\
		\Circled{3} Wrap the dyneema around the servo pulley \\ until taut. \\
		\Circled{!} You can adjust the initial configuration later\\ zeroing the servo motor.\\ 
		\Circled{4} Screw the M2.5x15 to the AX12 servo.
    	\end{tabular}
	\end{minipage}
	\hspace{0.5cm}	
	\begin{minipage}[b]{0.50\linewidth}
	\begin{tabular}{ c }
		
    	\end{tabular}
  	\end{minipage}
};
\node[mytitle, right=10pt] at (box.north west) {7.7.2 };
\end{tikzpicture}%
\end{center}

\newpage

\subsection{Standard Servo}

\begin{table}[ht!]
  	\begin{minipage}[b]{0.50\linewidth}\centering
	\scalebox{0.97}{
	\begin{tabular}{ | c | c |}
		\hline
		{\bf{Part}} & {\bf{Qty}}\\ \hline
		Robot Base StdServo & 1 \\ \hline
		servoPulleyStd1 & 1 \\ \hline
		servoPulleyStd2 & 1 \\ \hline
		servoPulleyStd3 & 1 \\ \hline
		Hitec HS-311 & 1 \\ \hline
		servoScrew & 1 \\ \hline
		M3x12 & 4 \\ \hline
		M3Washer & 4 \\ \hline
		M3Nut & 4 \\ \hline
    	\end{tabular}
	}
	\end{minipage}
	\hspace{0.5cm}	
	\begin{minipage}[b]{0.50\linewidth}\centering
	\scalebox{1}{
	\begin{tabular}{ | c |}
		\hline
 		\multicolumn{1}{|c|}{{\bf{Tools}}} \\
		\hline
		Acrylic Glue \\ \hline
		Allen Wrench\\ \hline
    	\end{tabular}
	}
  	\end{minipage}
\end{table}

\vspace{0.2cm}

\begin{center}
\begin{tikzpicture}
\node [mybox] (box){%
  	\begin{minipage}[b]{0.50\linewidth}\centering
	\begin{tabular}{ c }
		
    	\end{tabular}
	\end{minipage}
	\hspace{0.5cm}	
	\begin{minipage}[b]{0.50\linewidth}
	\begin{tabular}{ l }
		\Circled{1} Center the servoPulleyStd parts \#1,2.\\
		\Circled{2} Glue the two parts with acrylic glue.\\
		\Circled{3} Center the servoPulleyStd parts \#1-2,3.\\
		\Circled{4} Glue the two parts with acrylic glue.\\
		\Circled{!} Press all parts together to achieve\\ better gluing. \\ 
		\Circled{5} Insert the edge of the Dyneema inside\\ the anchor hole of the servoPulleyStd part \#3.\\
		\Circled{6} With the edge of the Dyneema and the M3Nut \\ do multiple surgeon's knots. \\
		\Circled{7} Wrap the dyneema around the servo pulley \\ until taut. \\
		\Circled{!} You can adjust the initial configuration later\\ zeroing the servo motor.\\ 
		\Circled{8} Screw the servoScrew to the Hitec HS-311. \\
    	\end{tabular}
  	\end{minipage}
};
\node[mytitle, right=10pt] at (box.north west) {7.8.1};
\end{tikzpicture}%
\end{center}

\newpage

\subsection{Robot Flange for Robot Base with AX12 Servo}

\begin{table}[ht!]
  	\begin{minipage}[b]{0.50\linewidth}\centering
	\scalebox{0.97}{
	\begin{tabular}{ | c | c |}
		\hline
		{\bf{Part}} & {\bf{Qty}}\\ \hline
		flangeAX12 \#1 & 1 \\ \hline
		flangeAX12 \#2 & 1 \\ \hline
		flangeAX12 \#3 & 1 \\ \hline
		M3Spacer10 & 4 \\ \hline
		M3Spacer25 & 4 \\ \hline
		M3x10 & 4 \\ \hline
    	\end{tabular}
	}
	\end{minipage}
	\hspace{0.5cm}	
	\begin{minipage}[b]{0.50\linewidth}\centering
	\scalebox{1}{
	\begin{tabular}{ | c |}
		\hline
 		\multicolumn{1}{|c|}{{\bf{Tools}}} \\
		\hline
		Acrylic Glue \\ \hline
		Allen Wrench\\ \hline
		Open-End Wrench \\ \hline
    	\end{tabular}
	}
  	\end{minipage}
\end{table}

\vspace{0.5cm}

\begin{center}
\begin{tikzpicture}
\node [mybox] (box){%
  	\begin{minipage}[b]{0.50\linewidth}\centering
	\begin{tabular}{ c }
		
    	\end{tabular}
	\end{minipage}
	\hspace{0.5cm}	
	\begin{minipage}[b]{0.50\linewidth}
	\begin{tabular}{ l }
		\Circled{1} Center the flangeAX12 parts \#2,3.\\
		\Circled{2} Glue the two parts with acrylic glue.\\
		\Circled{3} Center the flangeAX12 parts \#1,2-3.\\
		\Circled{4} Glue the two parts with acrylic glue. \\
    	\end{tabular}
  	\end{minipage}
};
\node[mytitle, right=10pt] at (box.north west) {7.9.1};
\end{tikzpicture}%
\end{center}

\newpage

\subsection{Robot Flange for Robot Base with Standard Servo}

\begin{table}[ht!]
  	\begin{minipage}[b]{0.50\linewidth}\centering
	\scalebox{0.97}{
	\begin{tabular}{ | c | c |}
		\hline
		{\bf{Part}} & {\bf{Qty}}\\ \hline
		flangeStdServo \#1 & 1 \\ \hline
		flangeStdServo \#2 & 1 \\ \hline
		flangeStdServo \#3 & 1 \\ \hline
		M3Spacer10 & 4 \\ \hline
		M3Spacer25 & 4 \\ \hline
		M3x10 & 4 \\ \hline
    	\end{tabular}
	}
	\end{minipage}
	\hspace{0.5cm}	
	\begin{minipage}[b]{0.50\linewidth}\centering
	\scalebox{1}{
	\begin{tabular}{ | c |}
		\hline
 		\multicolumn{1}{|c|}{{\bf{Tools}}} \\
		\hline
		Acrylic Glue \\ \hline
		Allen Wrench\\ \hline
		Open-End Wrench \\ \hline
    	\end{tabular}
	}
  	\end{minipage}
\end{table}

\vspace{0.5cm}

\begin{center}
\begin{tikzpicture}
\node [mybox] (box){%
  	\begin{minipage}[b]{0.50\linewidth}\centering
	\begin{tabular}{ c }
		
    	\end{tabular}
	\end{minipage}
	\hspace{0.5cm}	
	\begin{minipage}[b]{0.50\linewidth}
	\begin{tabular}{ l }
		\Circled{1} Center the flangeStdServo parts \#1,2.\\
		\Circled{2} Glue the two parts with acrylic glue. \\
		\Circled{3} Center the flangeStdServo parts \#1-2,3. \\
		\Circled{4} Glue the parts with acrylic glue. \\
		\Circled{5} Continue as you see in the picture.
    	\end{tabular}
  	\end{minipage}
};
\node[mytitle, right=10pt] at (box.north west) {7.10.1};
\end{tikzpicture}%
\end{center}

\newpage

\subsection{Final Assembly of Robot Hand with AX12 Servo}

\begin{table}[ht!]
  	\begin{minipage}[b]{0.50\linewidth}\centering
	\scalebox{0.97}{
	\begin{tabular}{ | c | c |}
		\hline
		{\bf{Part}} & {\bf{Qty}}\\ \hline
		FlangeAX12  & 1 \\ \hline
		Robot Hand AX12 & 1 \\ \hline
		M3Washer & 4 \\ \hline
		M3x10 & 4 \\ \hline
    	\end{tabular}
	}
	\end{minipage}
	\hspace{0.5cm}	
	\begin{minipage}[b]{0.50\linewidth}\centering
	\scalebox{1}{
	\begin{tabular}{ | c |}
		\hline
 		\multicolumn{1}{|c|}{{\bf{Tools}}} \\
		\hline
		Allen Wrench\\ \hline
		Open-End Wrench \\ \hline
    	\end{tabular}
	}
  	\end{minipage}
\end{table}

\vspace{0.5cm}

\begin{center}
\begin{tikzpicture}
\node [mybox] (box){%
	
};
\node[mytitle, right=10pt] at (box.north west) {7.11.1};
\end{tikzpicture}%
\end{center}

\newpage

\subsection{Final Assembly of Robot Hand with Standard Servo}

\begin{table}[ht!]
  	\begin{minipage}[b]{0.50\linewidth}\centering
	\scalebox{0.97}{
	\begin{tabular}{ | c | c |}
		\hline
		{\bf{Part}} & {\bf{Qty}}\\ \hline
		FlangeStdServo & 1 \\ \hline
		Robot Hand stdServo & 1 \\ \hline
		M3Washer & 4 \\ \hline
		M3x10 & 4 \\ \hline
    	\end{tabular}
	}
	\end{minipage}
	\hspace{0.5cm}	
	\begin{minipage}[b]{0.50\linewidth}\centering
	\scalebox{1}{
	\begin{tabular}{ | c |}
		\hline
 		\multicolumn{1}{|c|}{{\bf{Tools}}} \\
		\hline
		Allen Wrench\\ \hline
		Open-End Wrench \\ \hline
    	\end{tabular}
	}
  	\end{minipage}
\end{table}

\vspace{0.5cm}

\begin{center}
\begin{tikzpicture}
\node [mybox] (box){%
	
};
\node[mytitle, right=10pt] at (box.north west) {7.12.1};
\end{tikzpicture}%
\end{center}

\vspace{2cm}
\begin{center}
{\Large Congratulations you have created a robot hand!!!}
\end{center}

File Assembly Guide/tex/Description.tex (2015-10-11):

\section{Introduction}

\indent In this technical report we present a series of design directions for the development of open-source, affordable robot hands, that are also:

\begin{itemize}
	\item{modular}
	\item{light-weight}
	\item{intrinsically-compliant}
	\item{underactuated}
\end{itemize}
 
The following sections describe how to construct a series of robot hands with the aforementioned features. For their development we use off-the-shelf materials and equipment that can be easily found in hardware stores. The proposed robot hands, efficiently grasp a series of everyday life objects and are considered to be general purpose, as they can be used for various applications. 

\begin{figure}[H]
 	\begin{center}

 	\end{center}
	\caption{Two different versions of the proposed robot hands are depicted.}
	\label{RobotHands}
\end{figure}

To name a few, some of the possible applications are: 1) for autonomous grasping and teleoperation/telemanipulation studies, 2) as end-effectors of humanoid robots, 3) for mobile and aerial vehicle platforms that can be modified to be grasping capable, 4) for educational purposes, as they provide a low-cost solution for highly intriguing robotics lessons, 5) or even as affordable myoelectric prostheses that will assist amputees in everyday life tasks, helping them regain part of their lost dexterity.  The presented robot hands have been developed through the \href{www.openbionics.org}{OpenBionics (www.openbionics.org)} initiative \cite{Liarokapis2014ASURRW}, which was inspired by the \href{http://www.eng.yale.edu/grablab/openhand/}{Yale Open Hand Project} \cite{Ma2013ICRA}.

\newpage

\section{Design}

\subsection{Robot Finger Structure}

 In this section we present the robot finger structure and we explain the design choices made. The proposed design is based on the following simple/bioinspired idea: to structurally reproduce the flexion/extension motions of human fingers, using steady elastomer materials (that introduce also compliance) for a passive extension and cables driven through low-friction tubes for the flexion. These design choices produce a simple mechanism capable to reproduce the agonist/antagonist behavior of human hand, exerting at the same time adequate forces. More details regarding the theoretical foundations and the design choices made can be found in \cite{Zisimatos2014IROS}.\\

\begin{wrapfigure}{r}{0.5\textwidth}
 	\vspace{10pt}
 	\begin{center}

 	\end{center}
 	\vspace{0pt}
 	\caption{The structure of the robot finger.}
	\label{Finger}
 	\vspace{0pt}
\end{wrapfigure}

For the elastomer material, we use appropriate silicone sheets which add adaptability to the structure and provide a more robust and stable behavior even when attempting to grasp objects of complex shapes \cite{DollarTM2006}. \\
The stiffness of the finger joints can be modeled as a stiffness matrix with non-zero values in its diagonal, which allows the robot finger to adapt to objects of different shapes. On the other hand, in manipulation tasks, the uncontrolled out-of-plane motion of the fingers, is typically undesired. In order to balance the two requirements we used a similar tendon routing with Awiwi Hand  \cite{GrebensteinThesis}, splitting from one tendon to two as you can see in Fig. \ref{Finger}. \\
Deformable material is attached at the fingertips. The deformations that arise during contact with the grasped object lead to larger contact areas, resulting in smoother contact force distributions and increased grasp stability, as discussed in \cite{deformableciocarlie2005}.
The rigid phalanges and some parts of the finger base were constructed with Plexiglas cut with a laser cutting machine. It should be noted though, that the hereby proposed design can be implemented with any kind of plastic and of course with the desired dimensions. For the assembly of the robot fingers we use fishing line and needles in order to stitch the silicone sheets onto the rigid links (the links have appropriate holes by design).\\
In order to minimize the friction in the tendon transmission system we use low-friction tubes and a pulley mounted inside the finger base. Therefore the Dyneema fishing line, used as flexor tendon, moves freely within the tendon routing system.\\

\newpage

\subsection{A Robot Hand Basis that Provides Modularity}

The proposed basis is equipped with 5 slots and can be used for attaching a total of four fingers, as depicted in Fig. \ref{Modular Base}. 
More specifically, robot hands with various geometries of finger base frames can be developed. Those hands are capable of grasping various everyday life objects and each one is specialized for executing different types of grasping tasks. This reflects the basic idea for the presented design, that someone can create multiple, low-cost, task-specific robot hands, instead of one that is complex and expensive.\\

\begin{figure*}[h!]
\begin{center}
\begin{tabular}{  c  c  }
{\bf{Two Fingers}} & {\bf{Three Fingers}} \\ 
&
 \\ 
{\bf{Four Fingers v1}} & {\bf{Four Fingers v2}}\\ 
&
\\ 
\end{tabular}
\end{center}
\caption{Different robot hands created using identical modular fingers and the robot hand basis. One two-fingered, one three-fingered and two versions of four-fingered robot hands are depicted.} 
\label{Modular Base}
\end{figure*}

\subsection{A Disk Shaped Differential Mechanism}

\begin{wrapfigure}{l}{0.5\textwidth}
 	\vspace{0pt}
 	\begin{center}

 	\end{center}
 	\vspace{0pt}
 	\caption{The disk-shaped differential mechanism used in our robot hands.}
	\label{Disk}
 	\vspace{0pt}
\end{wrapfigure}

A disk-shaped differential mechanism has been developed to connect all the independent finger cables with the actuator (servo motor). The differential mechanism allows for independent finger flexions in case that one or multiple fingers have stopped moving, due to workspace constraints or in case that they are already in contact with the object surface. The mechanism is simple since it consists of a few simple parts (a Plexiglas disk, the dyneema fishing line and pulleys) and requires relatively small space in order to perform efficiently. Also, the differential disk moves in the air without being guided by sliders in an effort to minimize friction in the tendon routing system. Our differential mechanism is a variant of the whiffle tree (or seesaw) mechanism \cite{BirglenIJRR2006}.

\newpage

\section{Robot Hand Specifications}

In this section we present the robot hand specifications, i.e., the physical characteristics (Table \ref{Specs}, finger workspace and forces), design parameters 
(Table \ref{Parameters}) and grasping capabilities. All features refer to a 4-fingered robot hand with the Dynamixel AX12A actuator. All other designs presented, have lower weight but similar characteristics. \\

\subsection{Robot Hand Physical Characteristics}

In Table \ref{Specs}, the basic characteristics (dimensions and weight) of a four fingered robot hand version (V1) shown in Fig. \ref{Modular Base}, are presented.

\begin{table}[h!]
\caption{Robot Hand Physical Characteristics} 
\label{Specs}
\begin{center}
	\begin{tabular}{ | l | l | }
	\hline
 	\multicolumn{2}{|c|}{\bf{Four Fingered Robot Hand V1}} \\
	\hline
	Actuators & 1 \\ \hline
	Base Height (mm) & 110 \\ \hline
	Base Width (mm) & 77 \\ \hline
	Weight (g) & 280\\ \hline
    	\end{tabular}
\end{center}
\end{table}

\subsection{Design Parameters}

Our design is parametrized in the same way, reported in \cite{Ma2013ICRA}. The parameters are listed in Table \ref{Parameters}, to help the creator achieve optimized designs. More details can be found in \cite{DollarAR2005}. 

\begin{table}[h!]
\setlength{\belowcaptionskip}{-4pt}
\setlength{\abovecaptionskip}{-4pt}
\caption{Robot Hand Design Parameters} 
\label{Parameters}
\begin{center}
	\begin{tabular}{ | c | c | }
	\hline
	{\bf{Parameter}} & {\bf{Default Value}} \\ \hline
	KP, KD (flexure stiffness) (mm) &  3, 4 \\ \hline
	Stiffness Ratio & 2.37 \\ \hline
	KP Length, KD Length (mm) & 8, 8 \\ \hline
	RP, RD (transmission radii) (mm) & 2.25, 2.25 \\ \hline
	Transmission Ratio & 1 \\ \hline
	Finger Length (LP+LD) (mm) &  87.3 \\ \hline
	LP, LD (mm) & 44.1, 43.2 \\ \hline
	Linkage Ratio & 0.97 \\ \hline
	TP, TD (degrees) & 14 , 8 \\ \hline
	LB (mm) &  67\\ \hline
	Height (mm) &  12 \\ \hline
	Depth (mm) &  20 \\ \hline
	Pad Thickness (mm) & 6\\ \hline
    	\end{tabular}
\end{center}
\end{table}

Moreover, it should be noted that although in this project we are not proposing anthropomorphic robot hands, we used the metric presented in \cite{Liarokapis2013ICRA} in order to define the lengths for all phalanges and the relative positions of the finger base frames, maximizing humanlikeness of specific aspects of our design. Such a choice was made based on the hypothesis, that even if we design our simple robot hands as anthropomorphically as possible, we will maximize their ability to grasp objects created for the human hand. For our design we have used identical robot fingers following the dimensions of human index finger and for the distance between the opposing finger base frames we have selected the distance between the CMC of the thumb and the MCP of the index. This distance can be obtained using hand anthropometry studies \cite{BuchholzErgonomics1992}. More details can be found in \cite{Zisimatos2014IROS}. A recent study regarding prosthetic fingers can be found in \cite{Liarokapis2014EMBC}. 

\vspace{1cm}

\subsection{Finger Workspace}

The fingers' workspace is presented in Fig \ref{workspace}. The ratio graph between the first and the second angle is depicted in Fig. \ref{ratio}. The joint angles were captured experimentally, using markers at the joints and a vision system.

\begin{figure*}[h!]
\begin{center}
	
\end{center}
\caption{ The finger workspace.} 
\label{workspace}
\end{figure*}

\begin{figure*}[h!]
\begin{center}
	
\end{center}
\caption{The evolution of the ratio between the two angles. The ratio approximates a constant value of 2.86 (red line).} 
\label{ratio}
\end{figure*}

As we can see in Fig. \ref{workspace}, the proximal phalanx closes faster than the distal phalanx. This was achieved by selecting specific values of stiffness (KP, KD) for the two flexure joints (see Table \ref{Parameters} for details). Such a choice leads to more robust power grasps, as discussed in \cite{DollarTM2006}.

\vspace{1cm}

\subsection{Force Exertion Capability of Robot Fingers}
In order to evaluate the force exertion capability of the robot fingers, we measured the maximum force applied by the robot fingertips (distal phalanx) in two different configurations, as depicted in Fig. \ref{force1} and Fig. \ref{force2}. For each configuration, multiple experiments where conducted. The red lines represent the mean values and the blue dotted lines the min and max values per configuration. The high force values correspond to the 30\% flexed case and reach 18N (peak), with a standard low-cost servo. More details can be found in \cite{Zisimatos2014IROS}.

\begin{figure*}[h!]
\begin{center}
\begin{tabular}{  c  }

\end{tabular}
\end{center}
\caption{Force exertion for the 30\% flexed configuration.}
\label{force1}
\end{figure*}

\begin{figure*}[h!]
\begin{center}
\begin{tabular}{  c  }

\end{tabular}
\end{center}
\caption{Force exertion for the 70\% flexed configuration.} 
\label{force2}
\end{figure*}

As you can see  in Fig. \ref{force1} and Fig. \ref{force2} the forces drop at the 45\% of the maximum force applied and then they remain constant. This phenomenon is caused by the viscoelastic behavior of the silicone sheets \cite{DollarThesis}. \\

\newpage

\subsection{Experimental Validation of Robot Hands Efficiency}
\begin{figure*}[ht!]
\begin{center}
\begin{tabular}{ c }
\begin{tabular}{ c  c  c  c  c }
	\bf{Aerial Gripper} & \bf{Two Fingered} & \bf{Three Fingered}\\
	{Two Phalanges} & {Two Phalanges} & {Two Phalanges}\\

	&
	&
	\\

	&
	&
	\\
\end{tabular}\\
\begin{tabular}{ c  c  c  c  c }
	\bf{Three Fingered} & \bf{Four Fingered} \\
	{Three Phalanges} & {Two Phalanges} \\

	&
	\\

	&
	\\
\end{tabular} \\
\end{tabular}
\end{center}
\caption{Different robot hand models and robot hands created with the design directions provided, are depicted. } 
\label{RobotHands}
\end{figure*}

In order to experimentally validate the efficiency of the aforementioned design, we have developed different types of robot hands depicted in Fig. \ref{RobotHands} and we have conducted various experiments, with different applications in mind. The videos of the conducted experiments, can be found at the following URLs:

\begin{center}
Different applications:
{\url{https://www.youtube.com/watch?v=yEANsfaE1gs}}\\
Autonomous grasp planning:
{\url{https://www.youtube.com/watch?v=xs2CC9QLuFc}}\\
Grebenstein test:
{\url{https://www.youtube.com/watch?v=bniHWeXpX0A}}\\
\end{center}

More details about the experiments and the possible applications, can be found in \cite{Zisimatos2014IROS}, as well as at the official website of the OpenBionics initiative:

\begin{center}
{\url{http://www.openbionics.org}}
\end{center} 

\newpage

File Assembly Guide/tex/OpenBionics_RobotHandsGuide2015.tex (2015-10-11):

\documentclass[a4paper]{report}

\usepackage[top=3cm, bottom=3cm, left=3cm, right=3cm]{geometry}

\usepackage{hyperref}
\usepackage{url}
\usepackage{cite}

\usepackage{tikz}
\usetikzlibrary{shapes,snakes}
\usepackage{amsmath,amssymb}

\usepackage{float}
\usepackage{wrapfig}

\usepackage[english]{babel}
\usepackage{array}
\usepackage{caption}
\usepackage{subcaption}
\usepackage{graphicx}
\usepackage{sidecap}
\usepackage{float}

\newcommand{\HRule}{\rule{\linewidth}{0.5mm}}
\renewcommand{\thesection}{\thepart \arabic{section}}

\usepackage{pict2e,picture}
\newsavebox\CBox
\newlength\CLength
\def\Circled#1{\sbox\CBox{#1}%
	\ifdim\wd\CBox>\ht\CBox \CLength=\wd\CBox\else\CLength=\ht\CBox\fi
	\makebox[1.2\CLength]{\makebox(0,1.2\CLength){\put(0,0){\circle{1.2\CLength}}}%
	\makebox(0,1.2\CLength){\put(-.5\wd\CBox,0){#1}}}}

\begin{document}

	% Define box and box title style
	\tikzstyle{mybox} = [draw=black, fill=white, thick, rectangle, rounded corners, inner sep=0.4cm]
	\tikzstyle{mytitle} =[fill=black,rectangle, rounded corners, text=white]

	\begin{titlepage}
	\begin{center}
		{ \Large \bfseries How to Create Affordable, Modular, Light-Weight, Underactuated, Compliant Robot Hands\\[0.5cm] }
                { \large Agisilaos G. Zisimatos, Minas V. Liarokapis, Christoforos I. Mavrogiannis,\\ George P. Kontoudis and Kostas J. Kyriakopoulos}

                \vspace{1.4in}

		\fbox{}

                \vspace{2in}

		{ \large Technical Report, Control Systems Lab\\
                   School of Mechanical Engineering, National Technical University of Athens \\[0.5cm] }

		{ \large Athens, January 2015 \\[0.5cm] }

	\end{center}
	\end{titlepage}

	\newpage

	\begin{minipage}{0.2\textwidth}
		
	\end{minipage}
	\begin{minipage}{0.8\textwidth}
		\begin{flushleft} \large        
			OpenBionics by \url{www.openbionics.org} is licensed under a  \href{https://creativecommons.org/licenses/by-sa/4.0/}{Creative Commons Attribution-ShareAlike 4.0 International License}.
		\end{flushleft}
	\end{minipage}

	\vspace{12cm}

\begin{center}
 
\end{center}

	{\Large \bfseries Contact: }\\

        \noindent Agisilaos G. Zisimatos, George P. Kontoudis and Kostas J. Kyriakopoulos are with the Control Systems Lab, School of Mechanical Engineering, National Technical University of Athens, 9 Heroon Polytechniou Str, Athens, 15780, Greece (email:\{el08087,mc11681,kkyria\}@mail.ntua.gr).\\

        \noindent Minas V. Liarokapis is with the Dept. of Mechanical Engineering and Materials Science, School of Engineering and Applied Science, Yale University, 9 Hillhouse Avenue, New Haven, CT, 06520, USA (email:minas.liarokapis@yale.edu).\\

        \noindent Christoforos I. Mavrogiannis is with the Sibley School of Mechanical \& Aerospace Engineering, Cornell University, Ithaca, NY, 14853, USA (email:cm694@cornell.edu).\\

	\noindent For any inquiry and/or suggestion you may contact: Agisilaos Zisimatos (email:el08087@mail.ntua.gr), Minas Liarokapis (email:minas.liarokapis@yale.edu). 

\newpage
\tableofcontents
\newpage
\include{Description}

%%%% Appendices %%%% 

\include{Appendix1}
\include{Appendix2}
\include{Appendix3}
\include{Appendix4}

%%%% Bibliography %%%%

\bibliographystyle{ieeetr} 
\bibliography{Ref}

\end{document}

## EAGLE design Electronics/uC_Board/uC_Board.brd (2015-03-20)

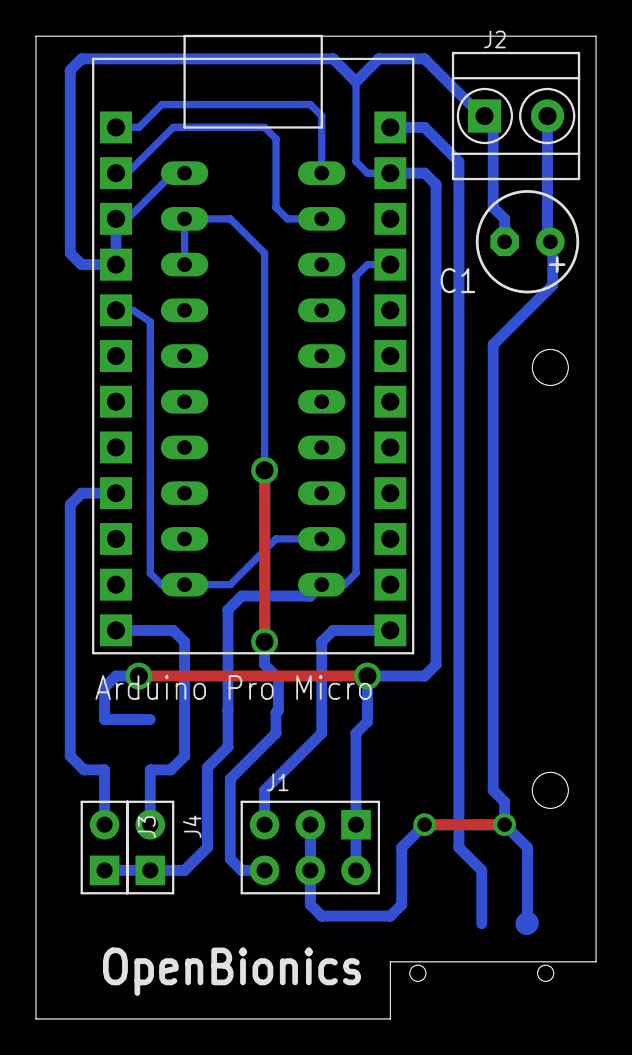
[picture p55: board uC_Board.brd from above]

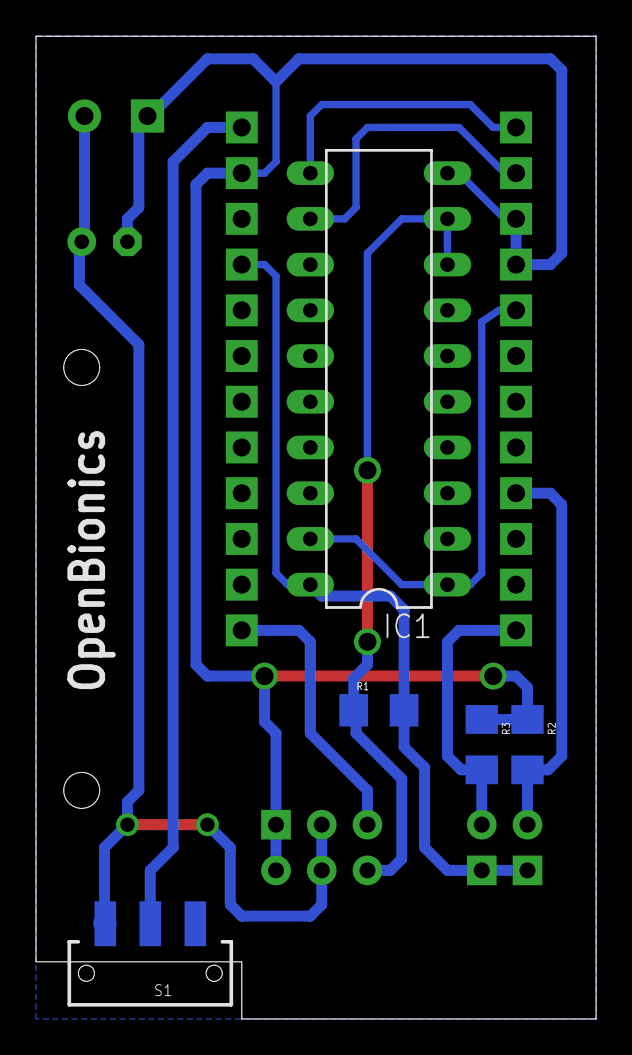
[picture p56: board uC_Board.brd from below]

Board: 2 copper layers, 31.1 x 54.6 mm, 11 parts (5 on the bottom side), 11 nets.

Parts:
ARDUINO_MICRO: ARDUINO_PRO_MICROARDUINO_BOARD; ARDUINO_MICRO_PRO
C1: 100u; E2,5-6
IC1: 74LS241N; DIL20
J1: 1; 2X3P-2.54-65/35MIL
J2: SCREW-TERMINAL-2P-3470070P1; 2P-3.5
J3: 2; 2P-2.54-65/35MIL
J4: 3; 2P-2.54-65/35MIL
R1, R2, R3: 10k; 1206
S1: 1; SWITCH-SPDT-SMD

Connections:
BUTTON1: ARDUINO_MICRO.9, J3.2, R2.2
BUTTON2: ARDUINO_MICRO.12, J4.2, R3.2
C_DATA: ARDUINO_MICRO.5, IC1.1, IC1.19
DATA: IC1.8, IC1.9, J1.4, R1.1
GND: ARDUINO_MICRO.3, ARDUINO_MICRO.4, ARDUINO_MICRO.23, C1.-, IC1.10, J1.1, J1.6, J2.1, R2.1, R3.1
IO1: ARDUINO_MICRO.13, J1.3
unnamed: ARDUINO_MICRO.24, S1.2
RX: ARDUINO_MICRO.2, IC1.12
TX: ARDUINO_MICRO.1, IC1.11
VCC: ARDUINO_MICRO.21, IC1.20, J3.1, J4.1, R1.2
VS: C1.+, J1.2, J1.5, J2.2, S1.3

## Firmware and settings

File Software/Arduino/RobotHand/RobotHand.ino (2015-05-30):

/*
This program is to control the robot hands of openbionics initiative.
URL: openbionics.org
Copyright (C) 2015  azisi(https://github.com/zisi)

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
You should have received a copy of the GNU General Public License
along with this program; if not, write to the Free Software Foundation,
Inc., 51 Franklin Street, Fifth Floor, Boston, MA 02110-1301  USA
*/

#include "Arduino.h"

/*
  MODE 1 for Standard Servo
  MODE 2 for AX12 Servo
*/
#define MODE 2

/*
  EXTENSION 0 without RobotHandExtension
  EXTENSION 1 with RobotHandExtension
*/
#define EXTENSION 0

#if MODE == 1
  #include <Servo.h>
  #define StdPin 10
  #define MaxPulse 2400 /* Pulse in us */
  #define MinPulse 544 /* Pulse in us */
  #define MaxAngle 218 /* Full rotation in deg */
  #define MaxVel 300 /* Max Velocity deg/s */
  Servo StdServo;
#elif MODE == 2
  #include <DynamixelSerial.h>
  #define DynPin 2
  #define MaxPos 1023
  #define MinPos 0
  #define MaxAngle 300 /* Full rotation in deg */
  #define DynBaudRate 1000000
  #define ID 1
  #define MaxTorque 1023
  #define DynVel 0.666   /* deg/s */
  #define MaxVel 350 /* Max Velocity */
#endif

#if EXTENSION == 1
  #define OpenButton 6
  #define CloseButton 9
  #define StepAngle 2
#endif

#define BaudRate 115200
#define BufferSize 256

void setup();
void loop();
void GetServoState(void);
void MoveServoPosition(float GoalPos);
void MoveServoVelocity(float GoalVl);
double signal2deg(int Signal);
int deg2signal(double deg);
boolean isNumber(char *input);

struct ServoState {
  double Pos;
  double Load;
};

void setup()
{
  /* Initialize serial communication */
  Serial.begin(BaudRate);
  /* Initialize Standard Servo */
  #if MODE == 1
    StdServo.attach(StdPin);
    MoveServoPosition(0);
  /* Initialize Dynamixel Servo */
  #elif MODE == 2
    Dynamixel.begin(DynBaudRate, DynPin);
    Dynamixel.ledStatus(ID, ON);
    Dynamixel.setID(1, ID);
    Dynamixel.setMaxTorque(ID, MaxTorque);
    delay(1000);
    MoveServoPosition(0);
    Dynamixel.ledStatus(ID, OFF);
  #endif
  #if EXTENSION == 1
    pinMode(OpenButton, INPUT);
    pinMode(CloseButton, INPUT);
  #endif
}

void loop()
{
  #if EXTENSION == 0
    char Buffer[BufferSize];
    char IncomingByte;
    char *Data = Buffer;
    static float GoalPos = 0;
    static float GoalVl = 0;
    static int BufferCnt = 0;

    while (Serial.available() > 0)
    {
      IncomingByte = Serial.read();
      /* New data */
      if (IncomingByte == '\n')
      {
        Buffer[BufferCnt]=0;
        /* Set Position */
        if ((Buffer[0] == 'p' && Buffer[1] == 's') || (Buffer[0] == 'P' && Buffer[1] == 'S'))
        {
          strncpy(Data, Buffer+2, 100);
          if (isNumber(Data) && *Data != 0 && atof(Data) >= 0 && atof(Data) <= MaxAngle)
          {
            GoalPos = atof(Data);
            MoveServoPosition(GoalPos);
            /* Return 0 is OK */
            Serial.print("0");
            Serial.print("\n");
          }
          else
          {
            /* Wrong Command return -1 */
            Serial.print("-1");
            Serial.print("\n");
          }
          /* Reset Buffer Counter */
          BufferCnt = 0;
        }
        /* Set Velocity */
        else if ((Buffer[0] == 'v' && Buffer[1] == 'l') || (Buffer[0] == 'V' && Buffer[1] == 'L'))
        {
          strncpy(Data, Buffer+2, 100);
          if (isNumber(Data) && *Data != 0 && atof(Data) >= -MaxVel && atof(Data) <= MaxVel)
          {
            GoalVl = atof(Data);
            MoveServoVelocity(GoalVl);
            /* Return 0 is OK */
            Serial.print("0");
            Serial.print("\n");
          }
          else
          {
            /* Wrong Command return -1 */
            Serial.print("-1");
            Serial.print("\n");
          }
          /* Reset Buffer Counter */
          BufferCnt = 0;
        }
        /* Get State of Servo Motor */
        else if ((Buffer[0] == 'g' && Buffer[1] == 's') || (Buffer[0] == 'G' && Buffer[1] == 'S'))
        {
          strncpy(Data, Buffer+2, 100);
          if (*Data == 0)
          {
            GetServoState();
          }
          else
          {
            /* Wrong Command return -1 */
            Serial.print("-1");
            Serial.print("\n");
          }
          /* Reset Buffer Counter */
          BufferCnt = 0;
        }
        else
        {
          /* Reset Buffer Counter */
          BufferCnt = 0;
          /* Wrong Command return -1 */
          Serial.print("-1");
          Serial.print("\n");
        }
      }
      else
      {
        /* Fill the buffer with incoming data */
        Buffer[BufferCnt] = IncomingByte;
        BufferCnt ++;
      }
    }
   #elif EXTENSION == 1
     static int OpenState = 0;
     static int CloseState = 0;
     static float pos = 0;

     /* Read push buttons */
     OpenState = digitalRead(OpenButton);
     CloseState = digitalRead(CloseButton);
     delay(20);

     if (OpenState == HIGH && CloseState == LOW)
     {
       pos += StepAngle;
     }
     else if (OpenState == LOW && CloseState == HIGH)
     {
       pos -= StepAngle;
     }
     if (pos < 0)
       pos = 0;
     else if (pos > MaxAngle)
       pos = MaxAngle;
     MoveServoPosition(pos);
   #endif
}

/* Get state of motor */
void GetServoState()
{
  ServoState State;
  #if MODE == 1
    State.Pos = signal2deg(StdServo.readMicroseconds());
    State.Load = 0;
  #elif MODE == 2
    State.Pos = signal2deg(Dynamixel.readPosition(ID));
    State.Load = Dynamixel.readLoad(ID);
  #endif
  /* Send servo state to host PC */
  Serial.print("0");
  Serial.print(";");
  Serial.print(State.Pos);
  Serial.print(";");
  Serial.print(State.Load);
  Serial.print("\n");
}

/* Position control */
void MoveServoPosition(float GoalPos)
{
  int Signal;
  Signal = deg2signal(GoalPos);
  #if MODE == 1
    StdServo.writeMicroseconds(Signal);
  #elif MODE == 2
    Dynamixel.setEndless(ID, OFF);
    Dynamixel.move(ID, Signal);
  #endif
}

/* Velocity control */
void MoveServoVelocity(float GoalVl)
{
  int Signal;
  #if MODE == 1
    static float qprv = 0;
    float q;
    float dt = 0.003;
    q = qprv + GoalVl*dt;
    qprv = q;
    Signal = deg2signal(q);
    StdServo.writeMicroseconds(Signal);
  #elif MODE == 2
    Signal = abs(GoalVl/DynVel);
    Dynamixel.setEndless(ID, ON);
    if (GoalVl > 0)
      Dynamixel.turn(ID, RIGTH, Signal);
    else if (GoalVl < 0)
      Dynamixel.turn(ID, LEFT, Signal);
    else
      Dynamixel.turn(ID, LEFT, 0);
  #endif
}

/* Convert signal to degrees */
double signal2deg(int Signal)
{
  #if MODE == 1
    return (double(Signal-MaxPulse)/double(MinPulse-MaxPulse))*MaxAngle;
  #elif MODE == 2
    return (Signal*double(MaxAngle)/double(MaxPos));
  #endif
}

/* Convert degrees to signal */
int deg2signal(double deg)
{
  #if MODE == 1
    return MaxPulse+(MinPulse-MaxPulse)*deg/MaxAngle ;
  #elif MODE == 2
    return MaxPos*deg/MaxAngle;
  #endif
}

/* Check if is argument in number */
boolean isNumber(char *input)
{
  for (int i = 0; input[i] != '\0'; i++)
  {
    if (isalpha(input[i]))
      return false;
  }
   return true;
}

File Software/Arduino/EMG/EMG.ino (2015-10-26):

#include "Arduino.h"

#define EMGPin0 0
#define EMGPin1 0
#define MaxSignal 1023
#define MinSignal 0
#define MaxVolt 5 /* in V */
#define MinVolt 0
#define BaudRate 115200
#define BufferSize 256

void setup();
void loop();
void GetRawEMG();
double signal2deg(int Signal);

void setup()
{
  /* Initialize serial communication */
  Serial.begin(BaudRate);
}

void loop()
{
  char Buffer[BufferSize];
  char IncomingByte;
  char *Data = Buffer;
  static int BufferCnt = 0;

  while (Serial.available() > 0)
  {
    IncomingByte = Serial.read();
    /* New data */
    if (IncomingByte == '\n')
    {
      Buffer[BufferCnt]=0;
      /* Get State of Potentiometer */
      if ((Buffer[0] == 'g' && Buffer[1] == 's') || (Buffer[0] == 'G' && Buffer[1] == 'S'))
      {
        strncpy(Data, Buffer+2, 100);
        if (*Data == 0)
        {
          GetRawEMG();
        }
        else
        {
          /* Wrong Command return -1 */
          Serial.print("-1");
          Serial.print("\n");
        }
        /* Reset Buffer Counter */
        BufferCnt = 0;
      }
      else
      {
        /* Reset Buffer Counter */
        BufferCnt = 0;
        /* Wrong Command return -1 */
        Serial.print("-1");
        Serial.print("\n");
       }
      }
    else 
    {
      /* Fill the buffer with incoming data */
      Buffer[BufferCnt] = IncomingByte;
      BufferCnt ++;
    }
  }
}

/* Read analog inputs */
void GetRawEMG()
{
  /* If you use 2 EMGs uncomment the code */
  static int EMGValue0 = 0;
  /* static int EMGValue1 = 0; */
  
  EMGValue0 = analogRead(EMGPin0);
  /* EMGValue1 = analogRead(EMGPin1); */
  /* Send slider values to host PC */
  Serial.print("0");
  Serial.print(";");
  Serial.print(signal2deg(EMGValue0));
  /* Serial.print(";"); */
  /* Serial.print(signal2deg(EMGValue1)); */
  Serial.print("\n");
}

/* Convert signal to degrees */
double signal2deg(int Signal)
{
  return ((double)Signal*MaxVolt/(double)MaxSignal); /* in V */
}

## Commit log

2014-11-16 Changed the folders name
    [2-finger.SLDASM, 3-finger.SLDASM, 4-finger_v0.SLDASM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]
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2014-11-19 Add new PCB for RC and AX12 servo.
    [uC_Board.brd, uC_Board.sch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]
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2014-11-19 Add new CAD files for AX12 servo, PCB mount, STL for 3d-printer, to strengthen the robot base and to change the space of distal finger tip.
    [2-finger.SLDASM, 3-finger.SLDASM, 4-finger_v0.SLDASM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]
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2014-11-25 Repair the PCB,wrong connection with Rx in AX12 servo.
    [uC_Board.brd, uC_Board.sch]
2014-11-25 Add code and CAD files for robot hand extension.
    [RobotHandExtension.SLDPRT, RobotHandExtension.STL]
2014-11-28 Repair the support of servoPulleyStd parts.
    [ServoHorn.SLDPRT, servoPulleyStd.SLDASM, servoPulleyStd1-2.STL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]
2014-11-28 Add correct STL file for servoPulleyStd3.STL.
    [servoPulleyStd1.STL, servoPulleyStd3.STL]
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2015-03-19 Repair tube plates in finger base, distal and proximal.
    [FingerBase.STL, FingerDIP.STL, FingerPIP.STL]
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2015-03-23 Update common parts, Joint1, Joint2 and tubePIP with new robot hand parameters.
    [Joint1.SLDPRT, Joint2.SLDPRT, tubePIP.SLDPRT]
2015-03-23 Add stl files of 3d printed robot hand.
    [Base.SLDASM, BottomPlate.SLDPRT, Finger.SLDASM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]
2015-03-23 Add mount for kuka youbot source file and stl.
    [Mount_Kuka-Youbot.SLDPRT, Mount_Kuka-Youbot.STL, dovetail_female.STL]
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2015-04-04 Change the position of PCB slot, because the PCB is conflicted with the screws of the bottom plate.
    [BottomPlate.SLDPRT, BottomPlate.STL]
2015-04-04 Grew up the distance between the center of the part and the tendon hole.
    [servoPulleyAX12.SLDPRT, servoPulleyAX12.STL]
2015-04-04 Change the dimensions of the two parts, change the diameter of hole for M5 screw and add M5 nut housing in female part.
    [dovetail_female.SLDPRT, dovetail_male.SLDPRT]
2015-04-04 Remove the holes which arefasten the fingers, in order to make easiest the change of the fingers configuration.
    [TopPlate.SLDPRT, TopPlate.STL]
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2015-04-04 Change the thickness of stdServoBase1 part, change the height of stdServoBase2 part and update the assembly and stl files.
    [stdServoBase.SLDASM, stdServoBase1.SLDPRT, stdServoBase1.STL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]
2015-04-04 Update the 3d printed parts, assemblies and stl, after the changes in parts and RobotHandParameters.
    [Base.SLDASM, DifferentialDisk.SLDPRT, DifferentialDisk.STL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]
2015-04-04 Update the laser cutted parts and assemblies, after the changes in RobotHandParameters.
    [Base.SLDASM, BearingBase.SLDPRT, BottomPlate.SLDPRT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]
2015-04-04 Update the Joint1-2 and tubePIP after the changes of the RobotHandParameters, reduce the length of tubeMCP.
    [AX12.SLDASM, Joint1.SLDPRT, Joint2.SLDPRT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]
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2015-04-04 Add new common part, the screw M6 L12, which is used to couple the robot hand in PA10 robot arm.
    [90666A131 - ScrewM6L12LowProfile.SLDPRT]
2015-04-04 Add new common parts, the screw M5 L45 and M5 nut, which is used in flange coupling.
    [91292A195 - ScrewM5L45.SLDPRT, 91828A241 - NutM5.SLDPRT]
2015-04-04 Add new common part, screw M3 L12, which is used in the laser cutted robot finger base.
    [91292A114 - ScrewM3L12.SLDPRT]
2015-04-04 Add new common parts, screws M2 L6 and L8, which are used for coupling of servo motors with the bottomplate (L8), and for the mounting of the pulley AX12 servo motor (L6).
    [91292A831 - ScrewM2L6.SLDPRT, 91292A832 - ScrewM2L8.SLDPRT]
2015-04-04 Add new common part, non marring screw M3 L20, which is used to connect hex stand off M3 L12 with hex stand off M3 L30.
    [92605A109 - NonmarringM3L20.SLDPRT]
2015-04-04 Add new common part, the spacer ID3 L2, which is used to connect pulley in laser cutted bottom plate.
    [93657A001 - NylonSpacerID3L2.SLDPRT]
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2015-04-04 Rename FingerBasePin.SLDPRT to FingerBase.SLDPRT, change the height of the pillar, that placed in the TopPlate, to 3mm.
    [FingerBase.SLDPRT, FingerBase.STL, FingerBasePin.SLDPRT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]
2015-04-04 Move the inclination to one side of JointBase, in order to print easier than before and update the stl.
    [JointBase1.SLDPRT, JointBase1.STL, JointBase2.SLDPRT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]
2015-04-04 Add sockets in FingerDIP and FingerPIP for JointBase1-2, update the parts and stl after the changes in RobotHandParameters.
    [FingerDIP.SLDPRT, FingerDIP.STL, FingerPIP.SLDPRT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]
2015-04-04 Update the assemblies of the Finger.SLDASM and the RobotHand.SLDASM, after the changes and additions of the parts and the RobotHandParameters.
    [Finger.SLDASM, RobotHand.SLDASM]
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2015-05-30 Move the folder CAD/Laser Cutted to CAD/RobotHand/Laser Cutted.
    [Base.SLDASM, BearingBase.DXF, BearingBase.SLDPRT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]
2015-05-30 Add new Common part ScrewM5L22 and update the rest.
    [91828A241 - NutM5.SLDPRT, 92290A782 - ScrewM5L22.SLDPRT, Joint1.SLDPRT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]
2015-05-30 Move to CAD/RobotHand/3d Printed and change the pillars to 2mm.
    [Finger.SLDASM, FingerBase.SLDPRT, FingerBase.STL]
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2015-05-30 Move to CAD/RobotHand/3d Printed/ and add in TopPlate the holes for fingers.
    [Base.SLDASM, TopPlate.SLDPRT, TopPlate.STL]
2015-05-30 Move to CAD/RobotHand/3d Printed/ and update the RobotHand.SLDASM .
    [BottomPlate.SLDPRT, BottomPlate.STL, DifferentialDisk.SLDPRT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]
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2015-05-30 Serial communication patch. Check the validation of PS and VL commands (MaxAngle, MaxVel). Parse the GS command correctly ("GS 12" is not correct command).
    [RobotHand.ino]
2015-05-30 Add new files for robot hand extension interface.
    [RobotHandExtension.SLDPRT, RobotHandExtension.STL, RobotHandExtensionAssembly.SLDASM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]
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2015-10-05 Small fixes in robot finger parts.
    [Finger.SLDASM, FingerBase.SLDPRT, FingerBase.STL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]
2015-10-05 Small fixes in common parts.
    [Joint1.SLDPRT, Joint2.SLDPRT, tubePIP.SLDPRT]
2015-10-05 Small fixes in robot hand base.
    [Base.SLDASM, BottomPlate.SLDPRT, BottomPlate.STL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]
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2015-10-21 Update youbot mount and add new common part.
    [M4Nut.SLDPRT, Mount_Kuka-Youbot.SLDPRT, Mount_Kuka-Youbot.STL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]
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

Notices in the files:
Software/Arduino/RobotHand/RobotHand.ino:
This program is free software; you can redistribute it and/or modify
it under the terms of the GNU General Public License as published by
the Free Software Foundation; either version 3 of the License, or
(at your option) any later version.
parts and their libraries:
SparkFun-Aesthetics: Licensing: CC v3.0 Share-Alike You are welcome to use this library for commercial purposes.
